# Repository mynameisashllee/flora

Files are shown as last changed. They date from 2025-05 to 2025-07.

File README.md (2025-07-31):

# flora
a big crepe paper flower that blooms the closer you get to it and closes up when you're further away!

i wanted to make it because i make a lot of pipe cleaner/paper flowers so i was wondering if there was a way to make my flowers a hardware project. after some deliberation i figured this was a pretty fun thing to do for my first arduino project! i get to make it huge and pretty and crafty too, which is great.

## build
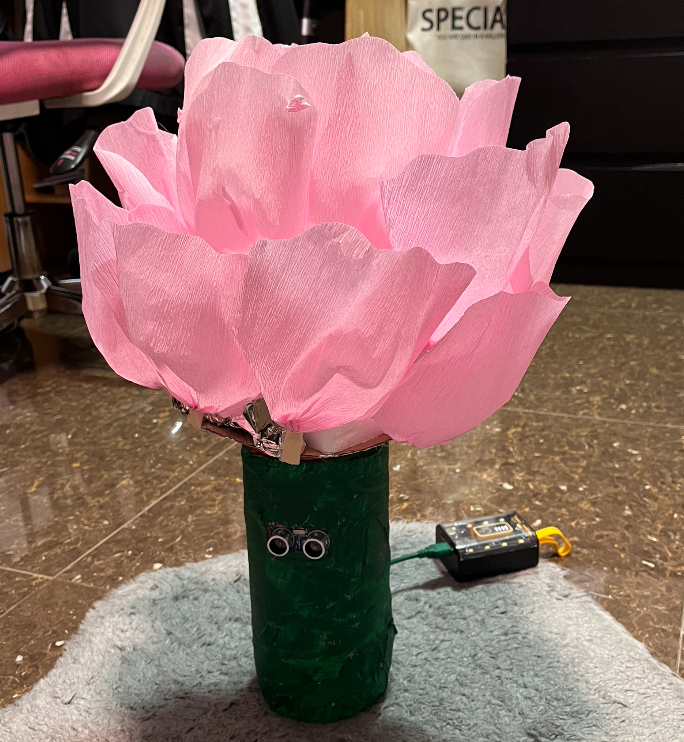
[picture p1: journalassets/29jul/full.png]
working


check out the demo on [youtube!](https://youtu.be/ohb0CGSC3Qs)

## screenshots
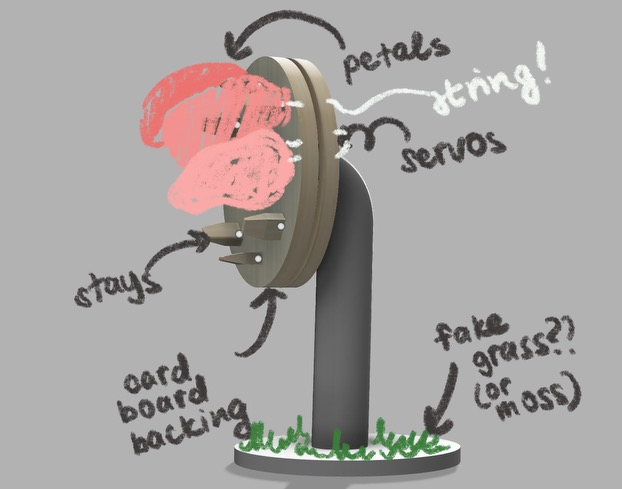
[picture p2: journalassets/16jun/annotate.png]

render of how the whole thing was planned to look - it's been changed up a bit!

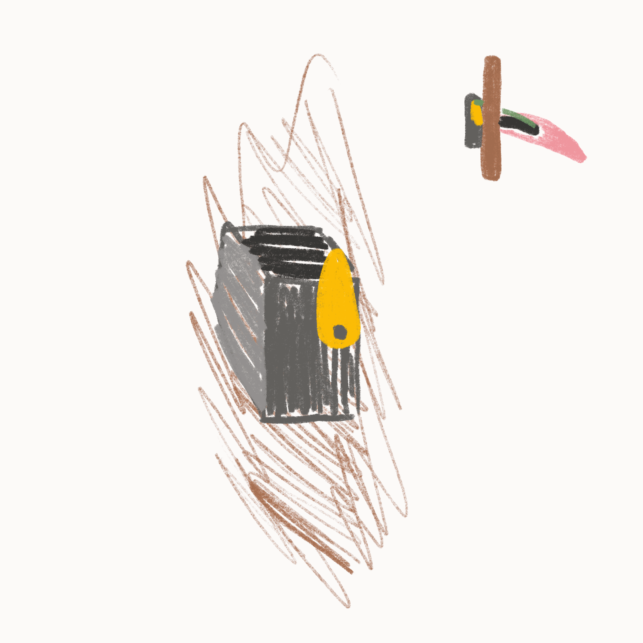
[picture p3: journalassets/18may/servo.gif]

how the servos turn

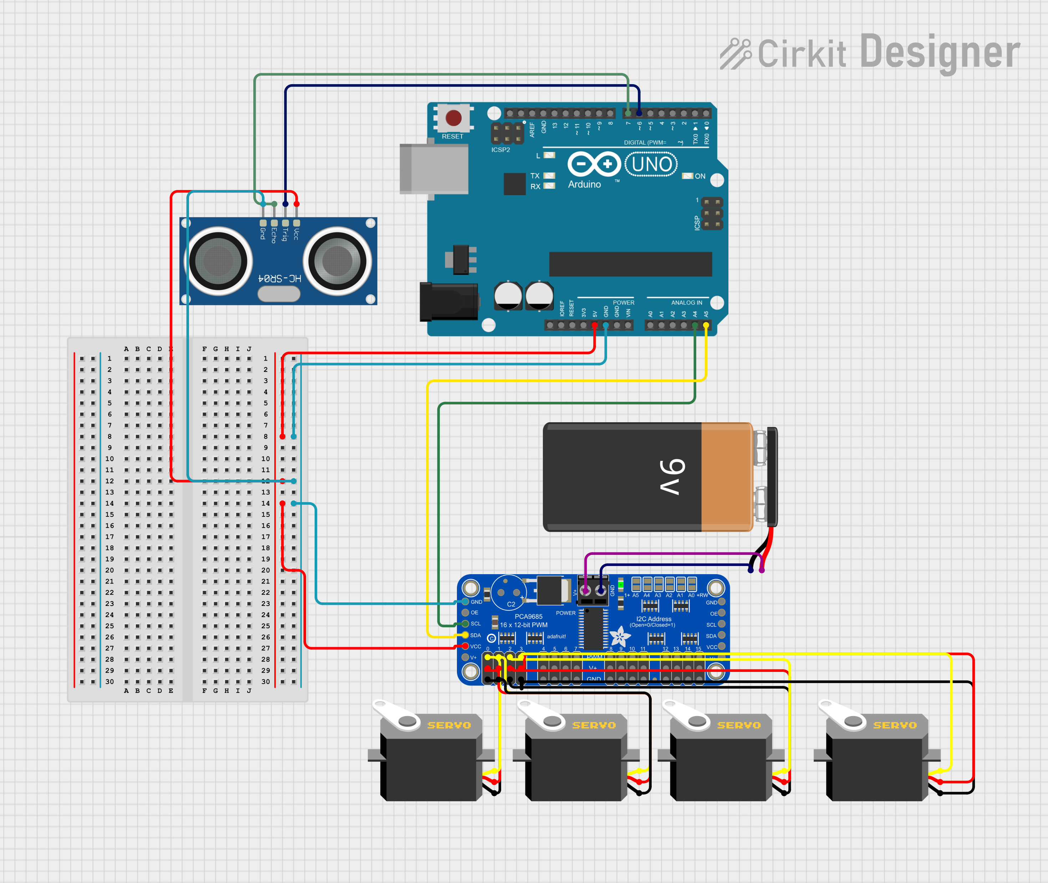
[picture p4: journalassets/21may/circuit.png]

wiring my arduino (4 aa batteries for power)

## bom
| **item name** 	| **purpose** 	| **qty** 	| **item source** 	| **item price** 	| **total price** 	|
|---	|---	|---	|---	|---	|---	|
| collar stays 	| holding up petals 	| 8 	| https://www.aliexpress.com/item/1005004401992941.html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 	| 1.78 	| 1.78 	|
| italian crepe paper (250x50cm) 	| petals 	| 5 	| https://www.aliexpress.com/item/1005007856841976.html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 	| 1.54 	| 7.70 	|
| fishing line 	| connecting petals to servo 	| 1 	| https://www.aliexpress.com/item/1005002121145052.html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 	| 0.80 	| 0.80 	|
| cardboard 	| base for flower parts 	| 1 	| recycled! 	| 0 	| 0 	|
| arduino uno 	| board to control other components 	| 1 	| https://www.aliexpress.com/item/1005007335850929.html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 	| 2.47 	| 2.47 	|
| PCA9685 16 channel driver 	| amplifying signal for servos 	| 1 	| https://www.aliexpress.com/item/1005005670283526.html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 	| 2.37 	| 2.37 	|
| breadboard 	| connecting components 	| 1 	| https://www.aliexpress.com/item/1005007174397080.html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 	| 1.17 	| 1.17 	|
| jumper wires (3 types) 	| connecting components 	| 20 x 3  	| https://www.aliexpress.com/item/1005007072081464.html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 	| 2.45 	| 2.45 	|
| HC-SR04 ultrasonic sensor 	| sensing distance 	| 1 	| https://www.aliexpress.com/item/1005007849944952.html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 	| 1.28 	| 1.28 	|
| MG 996R servos 	| to move the large petals 	| 4 	| https://www.aliexpress.com/item/1005004551732414.html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 	| 12.60 	| 12.60 	|
| battery case 	| to hold batteries 	| 1 	| https://www.aliexpress.com/item/4000859859685.html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 	| 0.98 	| 0.98 	|
| 4.7V batteries 	| to power servos 	| 2 	| already have 	| 0 	| 0 	|
| **total + shipping** 	| 	| 	| 	| 	| **35.19** 	|

## inspo
i actually had this idea myself but upon googling for more help i found this wonderful inspiration and absolutely had to mention it - [the tiktok](https://www.tiktok.com/@ingawoods.waight/video/7220271294841998638?lang=en). she made it in a *weekend* and i'm trying to model how my project looks after hers! huge props. we love women in stem.

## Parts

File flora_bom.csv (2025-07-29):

item name | purpose | qty | source | item price (USD) | total price (USD)
collar stays | holding up petals | 8 | https://www.aliexpress.com/item/1005004401992941.html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 | 1.78 | 1.78
italian crepe paper (250x50cm) | petals | 5 | https://www.aliexpress.com/item/1005007856841976.html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 | 1.54 | 7.7
fishing line | connecting petals to servo | 1 | https://www.aliexpress.com/item/1005002121145052.html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 | 0.8 | 0.8
cardboard | base for flower parts | 1 | recycled! | 0 | 0
arduino uno | board to control other components | 1 | https://www.aliexpress.com/item/1005007335850929.html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 | 2.47 | 2.47
PCA9685 16 channel driver | amplifying signal for servos | 1 | https://www.aliexpress.com/item/1005005670283526.html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 | 2.37 | 2.37
breadboard | connecting components | 1 | https://www.aliexpress.com/item/1005007174397080.html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 | 1.17 | 1.17
jumper wires (3 types) | connecting components | 20 x 3 | https://www.aliexpress.com/item/1005007072081464.html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 | 2.45 | 2.45
HC-SR04 ultrasonic sensor | sensing distance | 1 | https://www.aliexpress.com/item/1005007849944952.html?mp=1 | 1.28 | 1.28
MG 996R servos | to move the large petals | 4 | https://www.aliexpress.com/item/1005004551732414.html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 | 12.6 | 12.6
battery case | to hold batteries | 1 | https://www.aliexpress.com/item/4000859859685.html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 | 0.98 | 0.98
4.7V batteries | to power servos | 2 | already have | 0 | 0
total + shipping |  |  |  |  | 35.19

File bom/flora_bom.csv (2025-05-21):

item name | purpose | item source | item price | total price | qty
collar stays | holding up petals
italian crepe paper | petals
round mirror | centre of flower
fishing line | connecting petals to servo
cardboard | base for flower parts | recycled!
arduino uno | board to control other components
PCA968516 channel driver | amplifying signal for servos
breadboard | connecting components
jumper wires | connecting components
HC-SR04 ultrasonic sensor | sensing whether someone is there
MG 996R servos | to move the large petals
battery case | to hold batteries
AA batteries | to power servos
 |  |  |  | 0

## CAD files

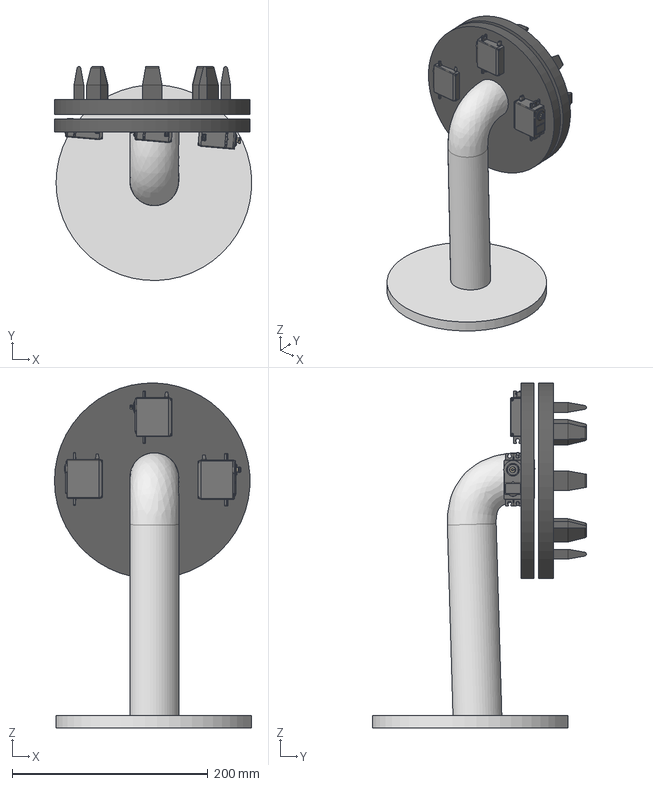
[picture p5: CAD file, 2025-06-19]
production/3d models/flora.step
201.5 x 218.7 x 352.7 mm

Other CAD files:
production/3d models/flora.3mf
production/3d models/flora.stl

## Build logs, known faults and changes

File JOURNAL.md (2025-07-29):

# journaling my journeying (33h total)

## 18-19 May (not very specifically documented sorry. i forgot)

okay! my idea for this whole project is basically a big ol pretty flower that opens up when you stand near it (so, arduino with distance sensor). i spent some time coming up with this idea because i really love making crafty flowers. i regularly make pipe cleaner/chenille and crepe paper flowers for my friends and birthdays and stuff!

if you don't believe me, here's my reference from valentine's day last year:
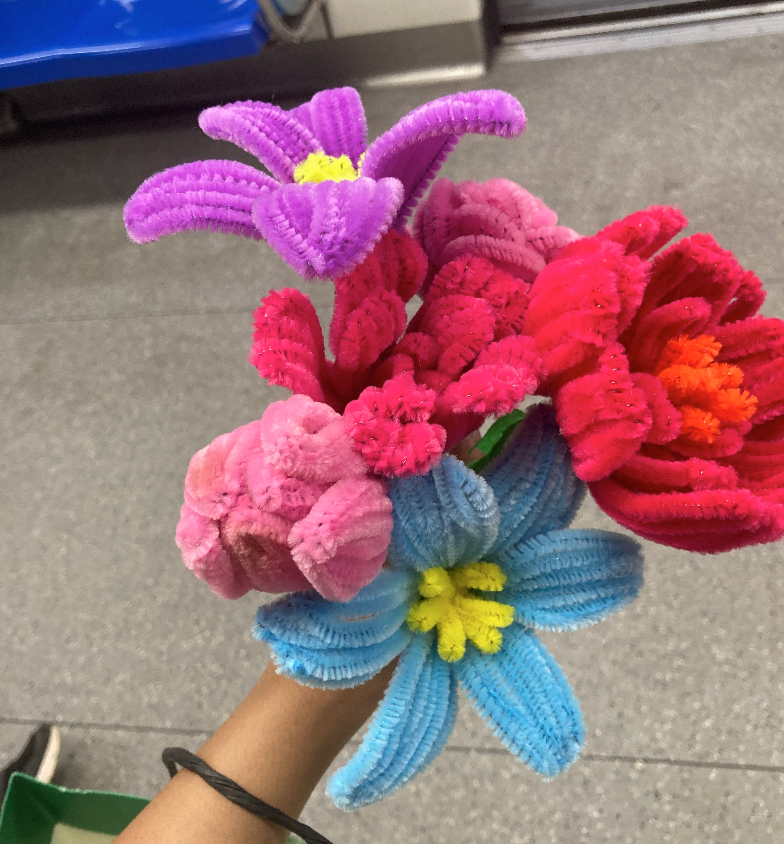
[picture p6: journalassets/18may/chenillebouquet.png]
bouquet


so i figured i'd motorise something like that. i found some stuff online like on pinterest but those flowers are like secretly protected by their makers so i'm going to have to improvise probably. i'm thinking of using an arduino, distance sensor and some servos.

this project is fairly mechanical, which means it's out of my pay grade for now. but we're here to learn! and of course my first step was to make a paper prototype-ish out of free foolscap i got handed outside my school.

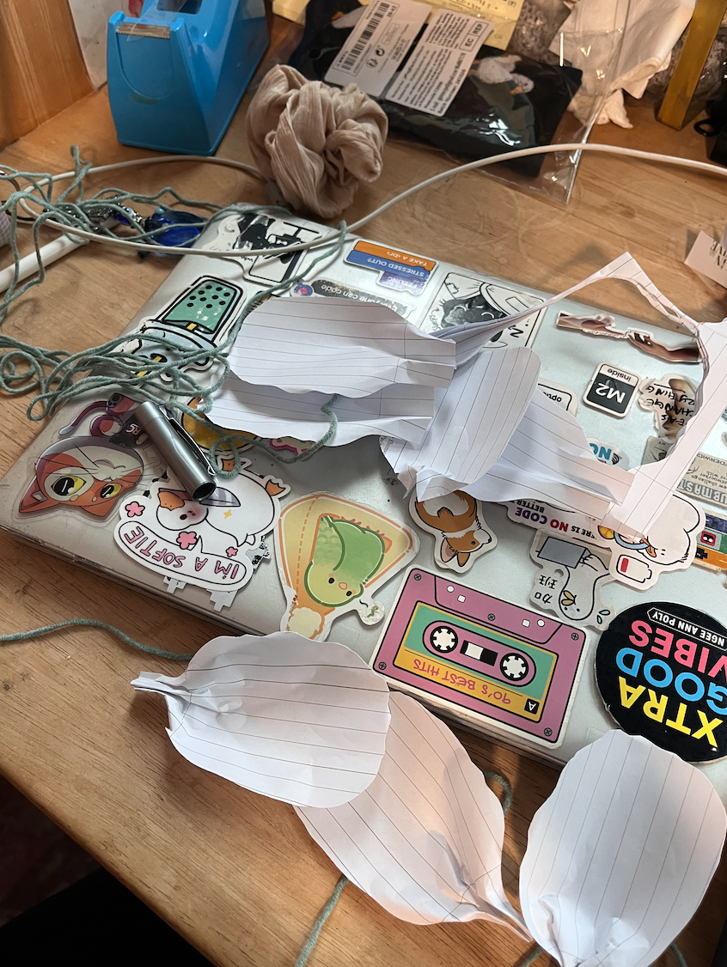
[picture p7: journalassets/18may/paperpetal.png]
paper petal

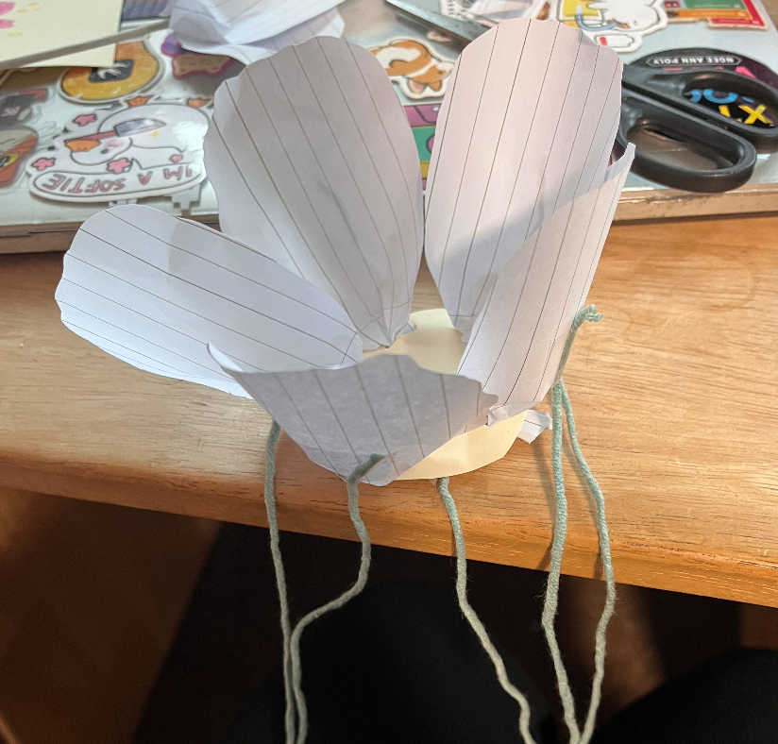
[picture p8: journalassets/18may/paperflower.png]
paper flower


so i cut out some rough outlines, attached it to a circle and tied some string. then i tried playing around with it to figure out how the servos could get it to open and i got a rough idea. 

animation!

i think for the actual thing instead of directly attaching the petals i'd want to use some bendy but half rigid plastic so it can snap back into place. because when i bend out the paper it crumples and doesn't go back to normal. and i think the string can be tucked into the circle too (maybe a bigger circle of foam board or smt) so there's more structure

alas, when i left for school and returned my paper flower was nowhere to be seen ): i guess someone assumed it was trash. rip

i guess over the next few days (or, i mean, after wednesday when i have an exam) i'd want to draw up a proper list of everything i need, wiring diagrams and maybe.. (ew) go on fusion.

update: i found a tiktok video of someone who actually did the same thing the internet is crazy. she put a mirror in the centre of the flower. i think that would be really cute.

time spent: 4 hours

## 21 May
just had an exam! yay! 2 things to do today - wiring and my bom

we did some wiring practice today - aka i learnt how to wire arduino stuff and got super intimidated. but it's actually not that deep surprisingly. i also found the models for the parts i plan to use which is good because bom!

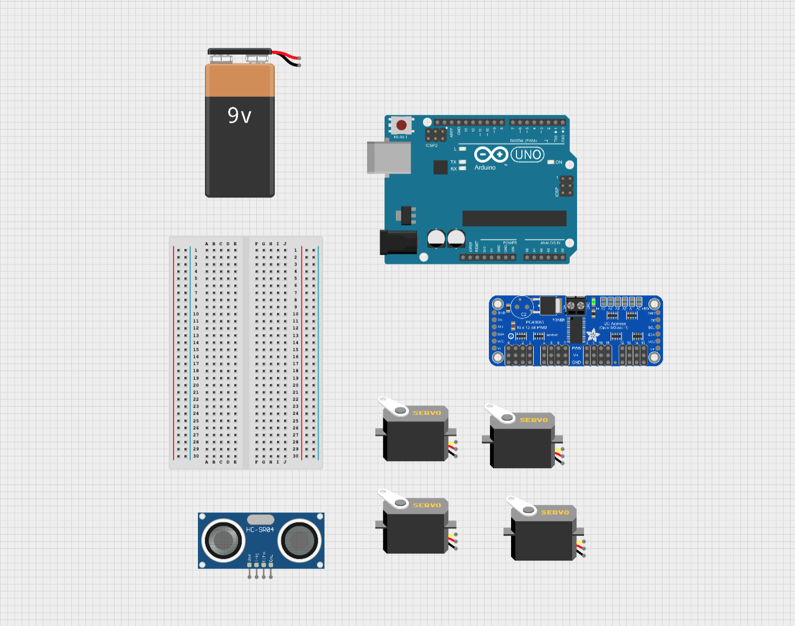
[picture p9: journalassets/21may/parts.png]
parts


after googling a bunch and looking through a lot of other peoples' arduino wiring designs i got this abomination (actually, this wasn't the worst. this was halfway through me detangling it)

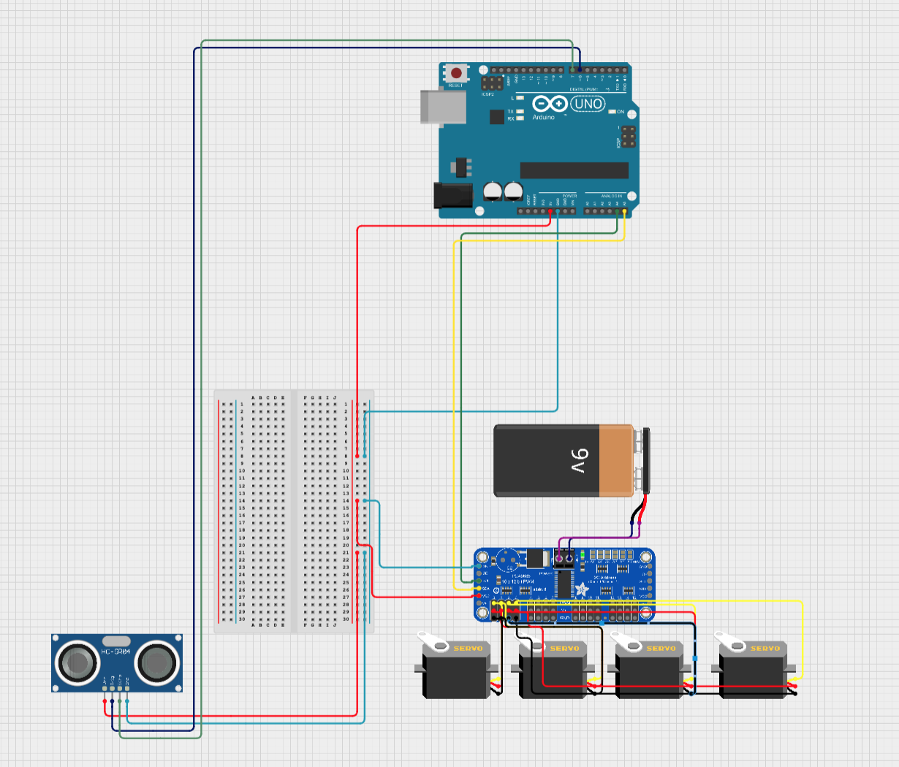
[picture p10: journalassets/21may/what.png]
oh


what the heck. i'm so sorry you had to see that.

anyway, we did it! 
final

not actually using a 9v battery, 6v instead (4 aa batteries) which hopefully works..! i panicked a lot about this and went to my friend who's on the school robo team for advice but she said it was okay
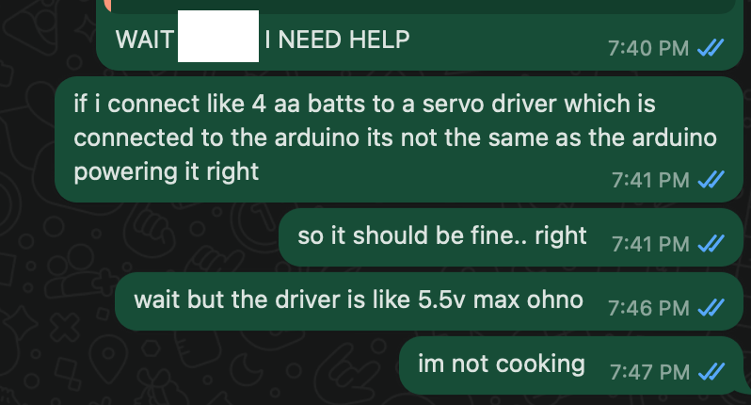
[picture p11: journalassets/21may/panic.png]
panic


things i learnt:
- connect everything to ground and 5v on the breadboard
- dont connect power to arduino

and did the bom too (sort of, lol)

time spent: 3 hours but spread out

## 16 Jun
oops, it's been a while.

today i finally bothered to 3d model the design - the *rough* design. i'm thinking of using acrylic pipes to connect flower and base because it will likely save me a lot of time on modelling and deciding the size.

here's me going absolutely insane while modelling because it took REALLY, REALLY long!
panic

anyway, this should basically show the structure of how my project will look. since a lot of my materials are like paper/cardboard/pipe, i don't want to be very exact with it because it'll likely take some trial and error to get it right. hopefully these dramatic shots (and my 3d model) can give a rough overview, though!

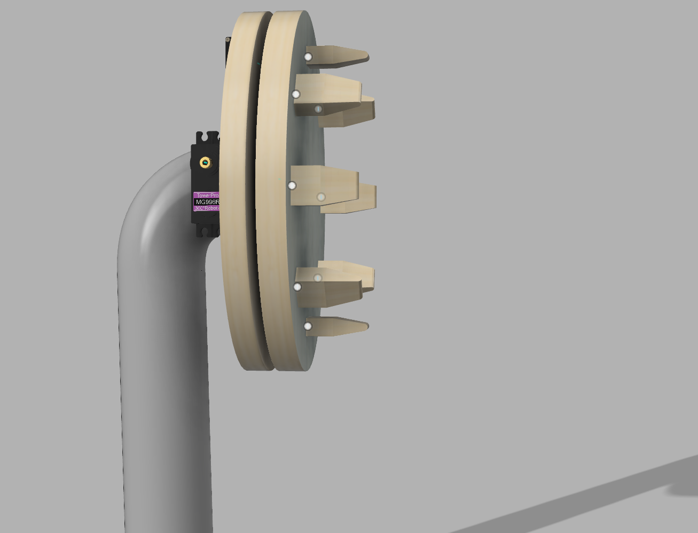
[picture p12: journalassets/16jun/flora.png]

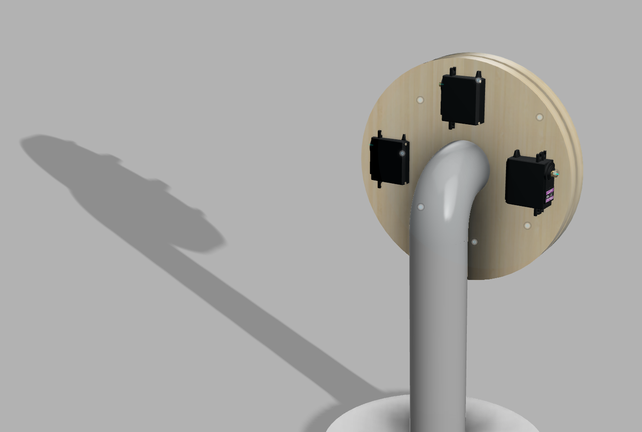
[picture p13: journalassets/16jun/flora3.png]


there are 8 props that will be used to hold up the petals, and string will attach the petals to the servos through the big cardboard centre. i wasted a lot of time trying to model the petals but here's a handy diagram of how they (and everything) should look.

diagram

i also did my firmware...! everything is in the production folder including wiring. truly appreciating online tutorials because they made my code and it's been forever since i used c++. i get why my friends who do robotics crash out all the time. i suspect that will be me soon.

next up i will finalise my bom... when i have the time.

time spent: 5 hours

## 17 Jun

took a break from studying today to finish up my BOM!

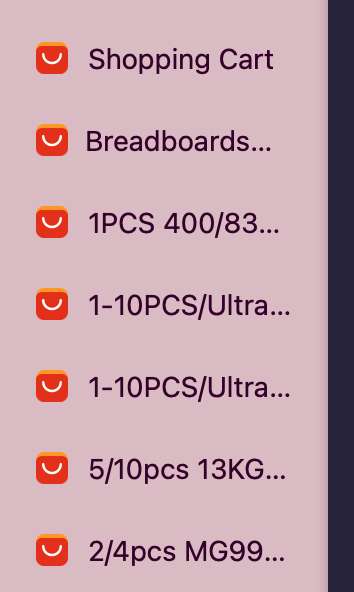
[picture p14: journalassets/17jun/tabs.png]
tabs


it has been done. i think i might submit now after a final few checks!

time spent: 1 hour

## 27 Jun

building!! my parts are all here and i was super excited to start.

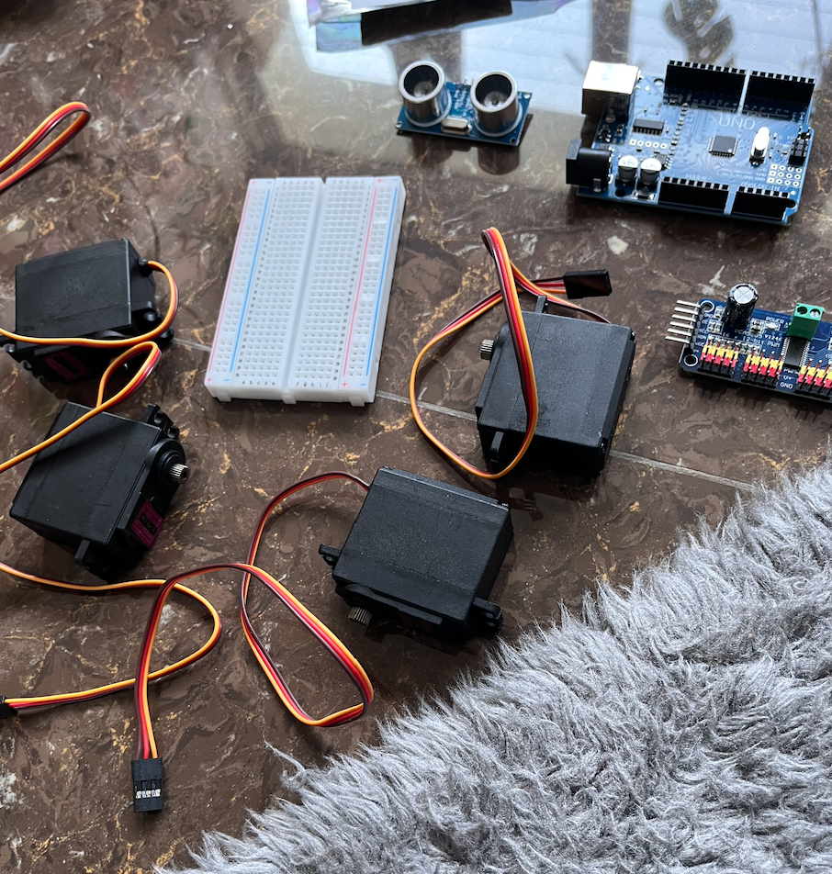
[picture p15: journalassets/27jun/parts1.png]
parts


first order of business was making sure my electronics work. so i took everything and wired it according to my diagram.

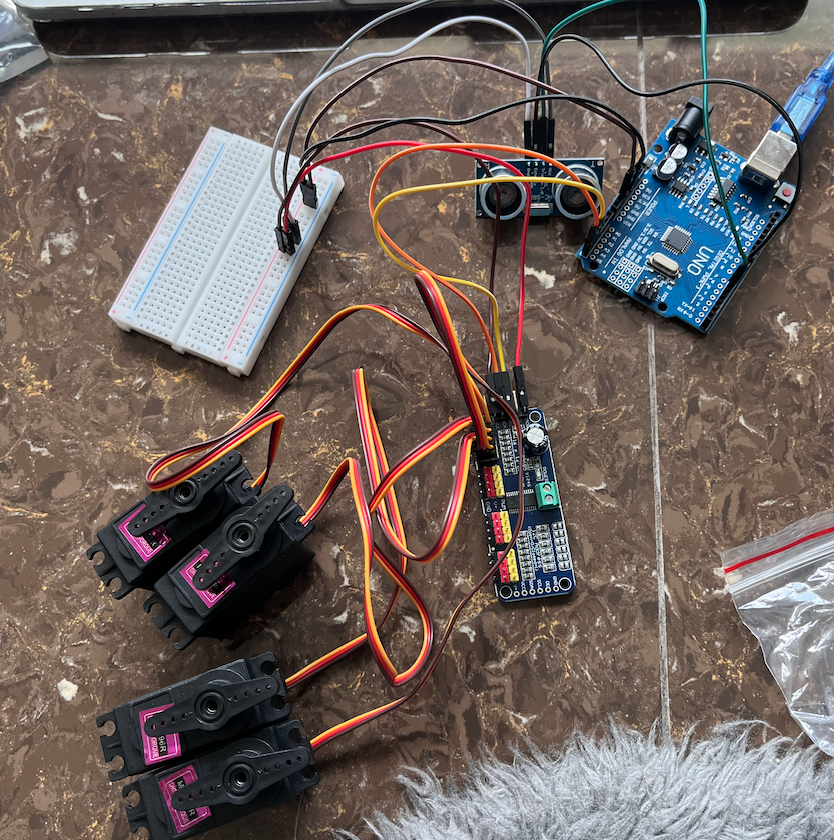
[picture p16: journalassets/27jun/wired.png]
wired


so initially i was freaking out because when i uploaded my firmware: 1. there were syntax errors (thanks c++) because i forgot semicolons and variable definitions like everywhere 2. MY SERVOS DIDN'T WORK 

so i started on debugging and i realised that, like a fool, i had forgotten to link up my pwm drivers to my battery pack! aha! what a great solution, i thought to myself, pulling out my battery case for 4 aa batteries. turns out i had ordered the wrong one. it was for much bigger 3.7V batteries.

in order to actually test my code and stop crashing out i just linked it to the arduino and disconnected it from power like every 20 seconds while hoping it didn't get fried. i'll probably go get some normal battery packs soon. i'm also regretting getting such short wires because i'm not super sure how everything's going to look on the whole flower structure BUT whatever.

once my servos worked, i had some more logic errors which made the servos reset every time they ran the open and close functions 

janked

(????)

so i set out to fix it with some irritating comments

code

after a bunch of hard work, here are my servos... working as intended! i'll probably have to cut the servo horn in half before i start assembling so it doesn't hit the cardboard.

working

also my crepe paper is here too, with surprisingly good quality. here's a petal model which is how it will look on the flower! (but bigger, probably)

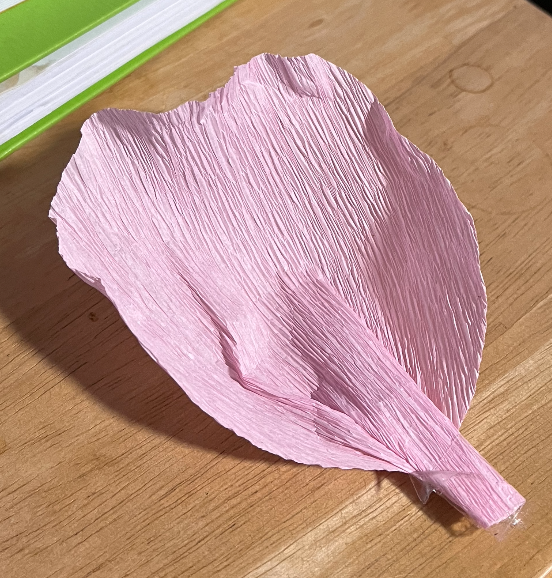
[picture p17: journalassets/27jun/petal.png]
petal


i spent a lot of time on the floor today. my knees hurt. i stabbed my finger with a pen. back for more next time.

time spent: 4 hours

## 5 July 
now that my circuit was ready, it was time to begin. today was the day i would finish it all. (or the base, anyway.) 

first off, i decided to actually cut the servo horns. using the power of wire cutters and sheer brute strength, i actually managed to do it all myself! 

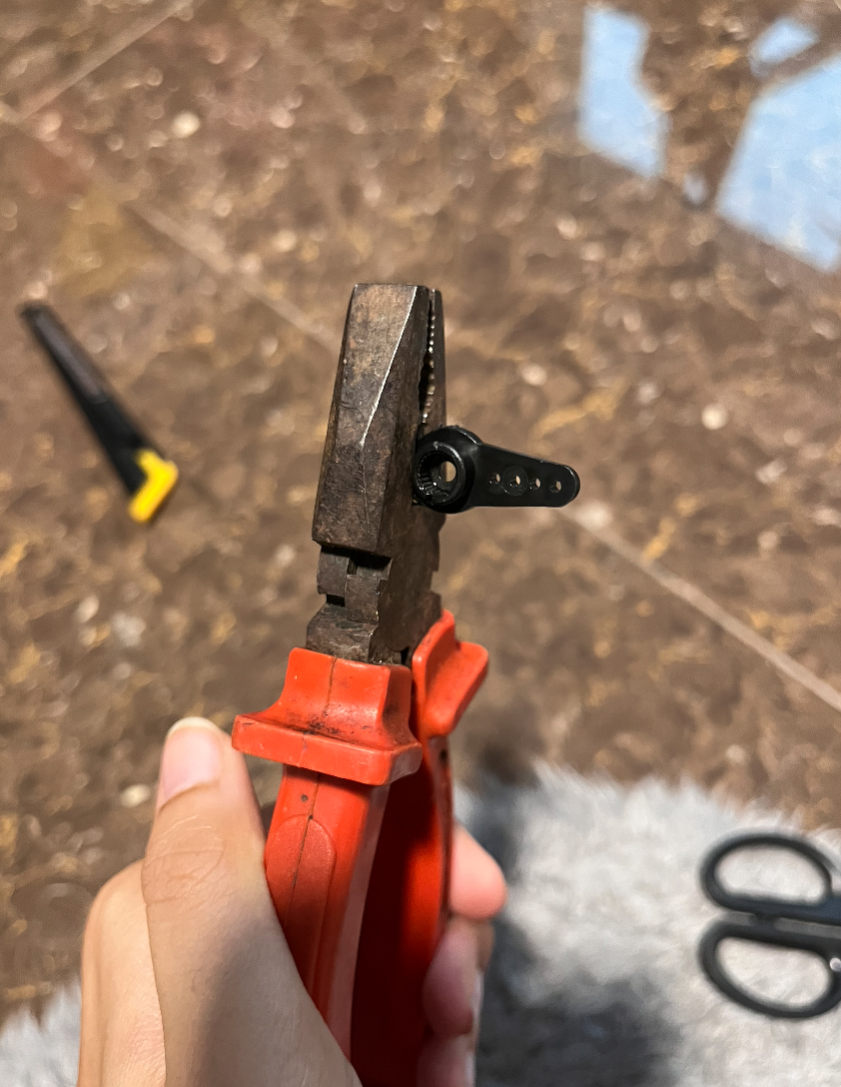
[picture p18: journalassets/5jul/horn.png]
horn


my hands were very, very red afterwards. i definitely do not recommend this step and if you ever find one sided servo horns you should just use those instead.

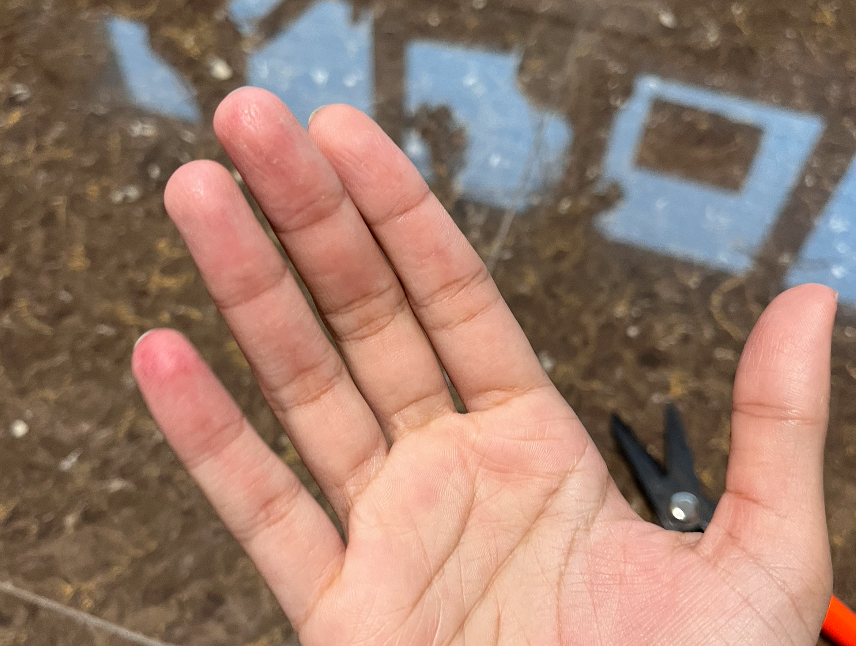
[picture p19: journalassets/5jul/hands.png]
hands


next, i scoured through my house for spare cardboard, and we had some nice thick boxes! the only problem was that there were folds at the places where i wanted to cut out the circle, but i figured i'd double layer the cardboard to make it sturdier.

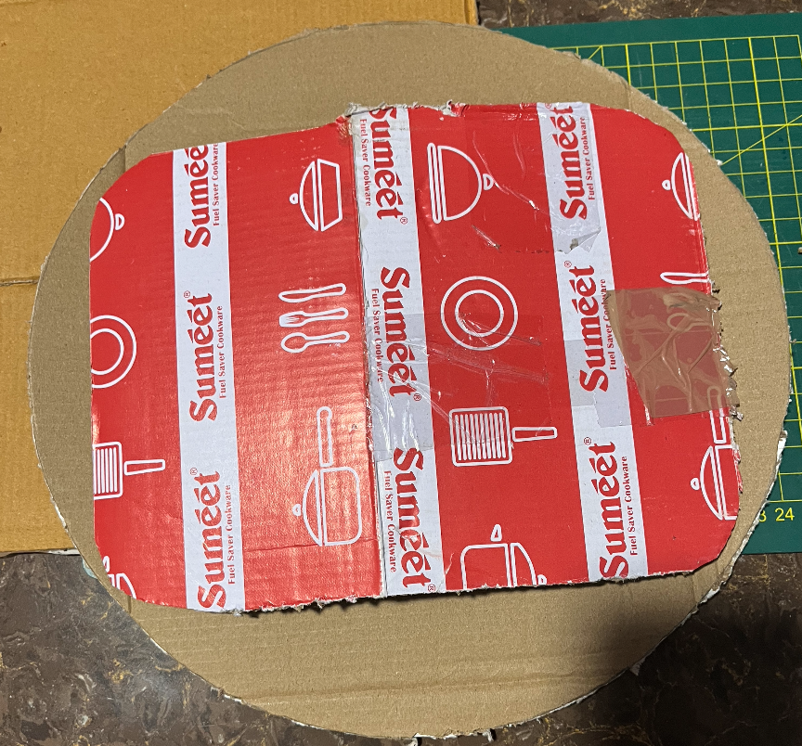
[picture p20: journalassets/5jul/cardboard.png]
cardboard


then i laid out the servos in the intended circlular orientation to figure out the correct way to open and close the petals. i made this high quality diagram to show the directions of the servos when the flower is 'open' for reference.

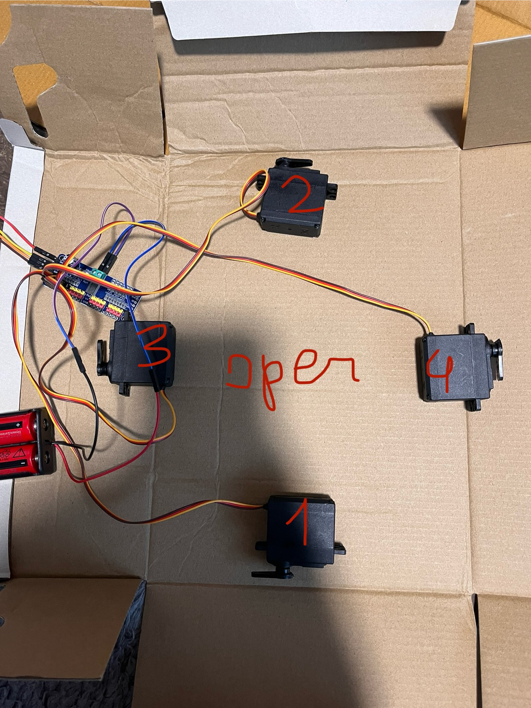
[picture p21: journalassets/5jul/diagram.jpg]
diagram


i then took to my collar stays with a heated screwdriver (the sad part was that it's a magnetic screwdriver with different heads and i think i ruined the magnetism by heating it) and poked some holes in them to tie the string. 

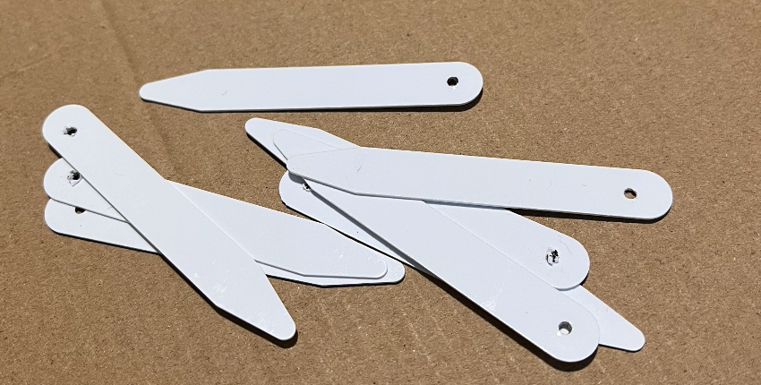
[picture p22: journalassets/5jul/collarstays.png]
collarstays


assembly time!! i taped the servos in positions and tied two collar stays to a servo with the fishing line. 

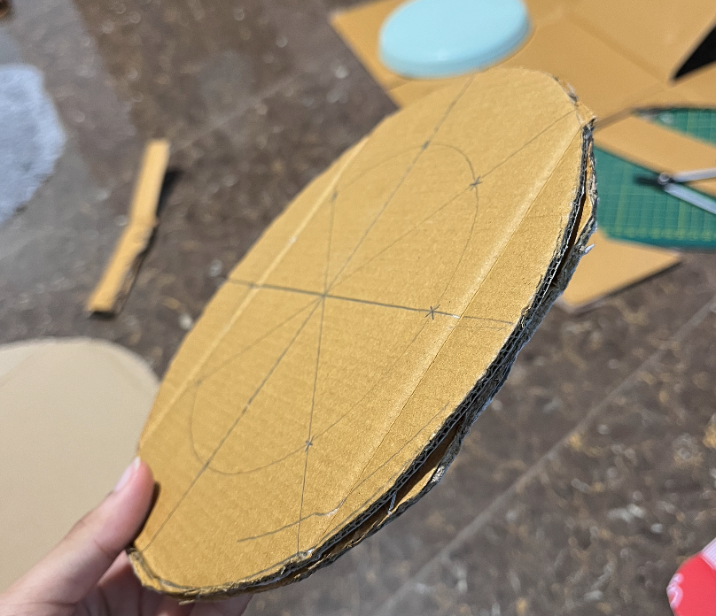
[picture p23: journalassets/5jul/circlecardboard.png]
circlecardboard


https://github.com/user-attachments/assets/06558860-657e-401c-917a-8a24dc6fcc48

when i powered up the servos i was like, woah! this is so cool! it works! 

https://github.com/user-attachments/assets/97546c10-0c78-4bb9-bc74-a5d542ef6f94

then i went oh no, because only half the collar stays were being pulled open. after analysing the front and back i realised that the servos were in a position where they were closer to one of the collar stays, so there wasn't an even distribution of torque between the two and one of the collar stays just closed up more.

once i fixed the orientation, i realised that my cardboard circle was really small and the servos would just knock into each other so i elevated two of them with a hot glued contraption of spare cardboard.

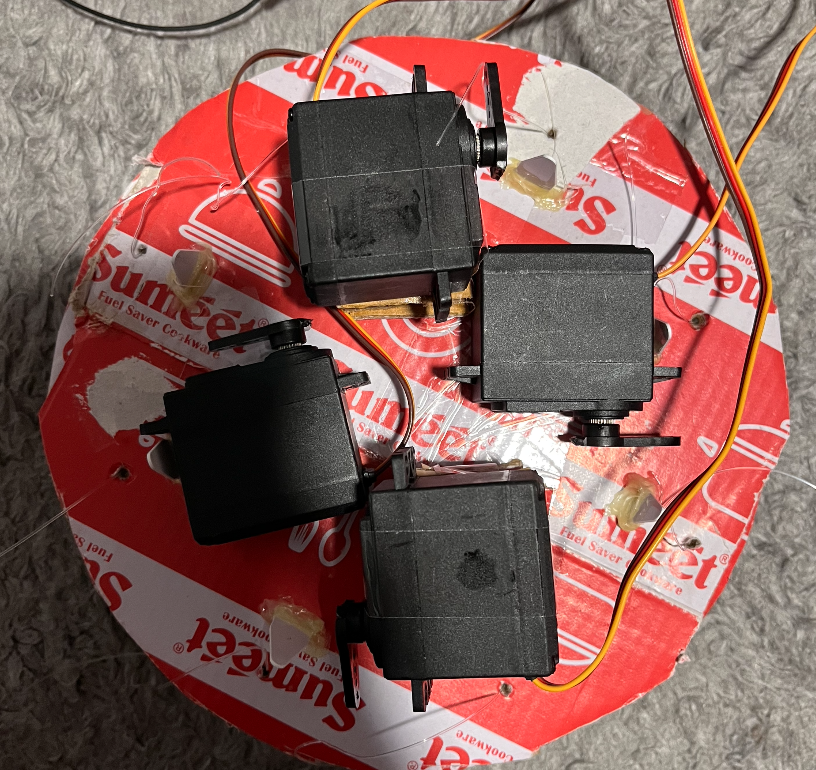
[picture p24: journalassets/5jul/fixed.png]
fixed

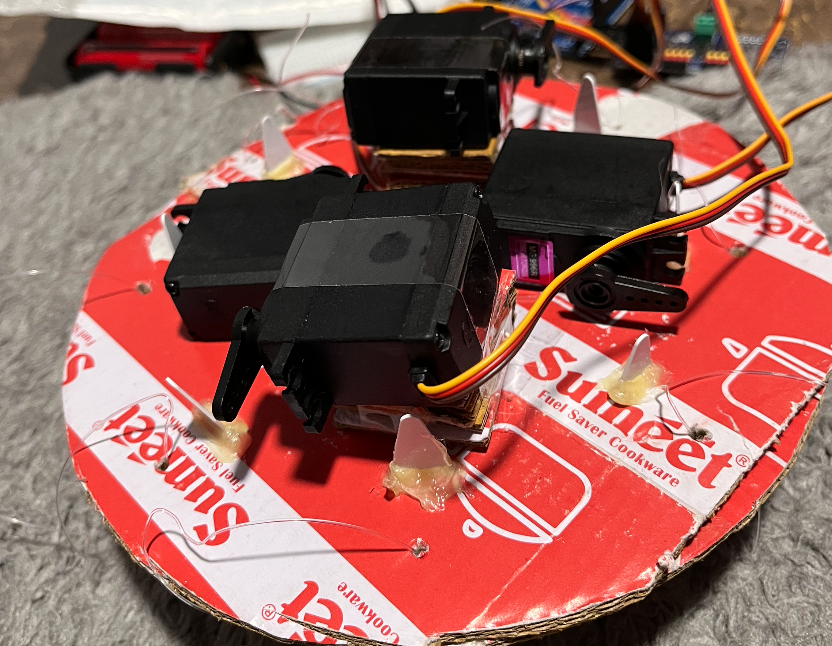
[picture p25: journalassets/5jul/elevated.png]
elevated


and voila!! it worked.

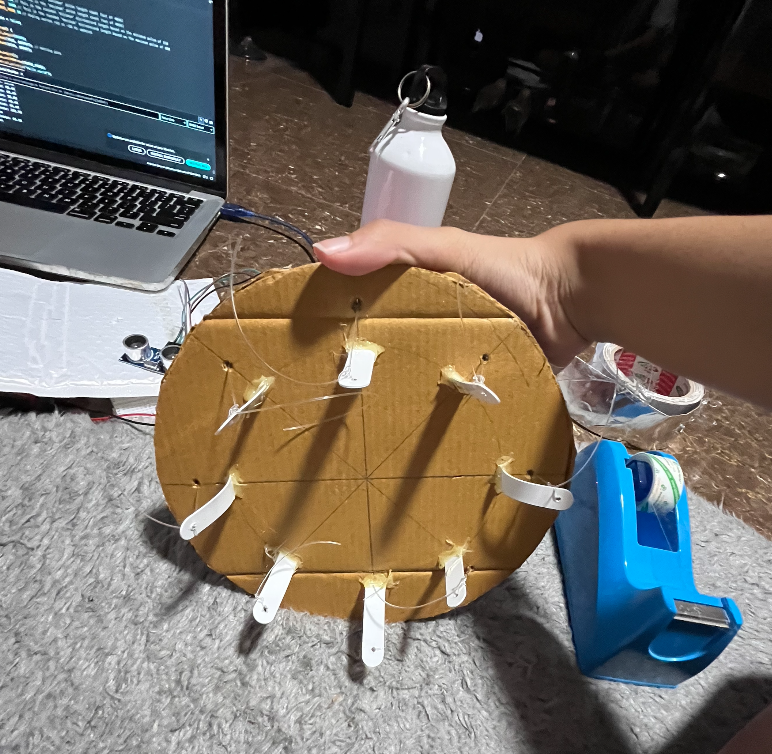
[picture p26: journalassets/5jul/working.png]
working


then i got to work securing everything properly with hot glue and my circuit kind of came apart. suddenly... once i rewired everything the servos JUST STOPPED WORKING. they heated up a lot and just didnt move at all even though power was going through the circuit. at this point it was 12am, and i was crashing out and just let it go. good night.

(8 hours)

## 7 July
so after consulting with the slack, i got really terrified that my servos were just totally fried. after checking my wiring properly i realised that i had just wired my servo driver into the wrong GPIO pin on my arduino. i felt like a fool. on the bright side, it works now! properly! but no day comes without its challenges, and today's challenge was that i tied some of the fishing lines too tight so one of the servos just popped off the base and some of the lines snapped. but once i fix this, it'll definitely work!

## 22 July
my first entry after getting back from undercity! i retied my lines and hot glued AND taped my servos properly to really ensure they stayed in place (because the cardboard stack i put the servo on was not stable enough. but now it is!).

and then on to my favourite (crafty) part... the petals! here's my flower with one attached.
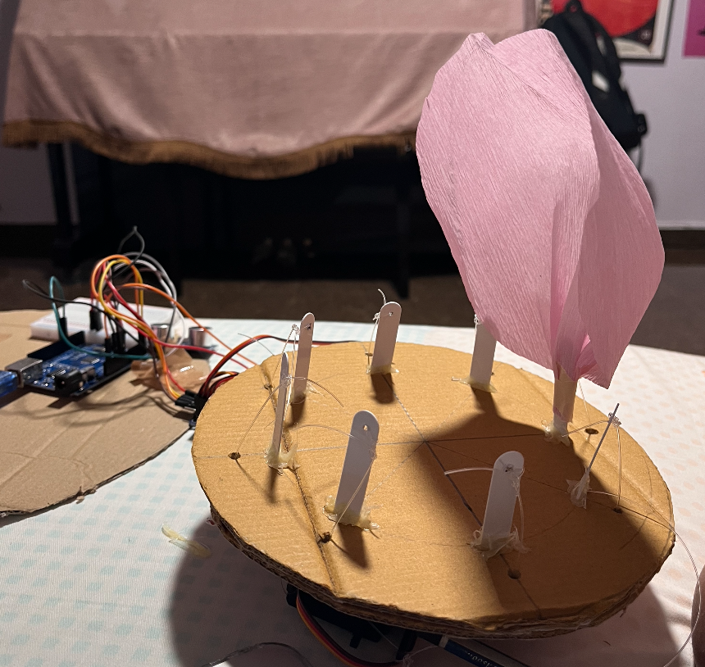
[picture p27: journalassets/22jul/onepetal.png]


and here's all 8 of the moving petals! in action!! i'm so excited honestly.

https://github.com/user-attachments/assets/9ec3462b-fdc6-45b9-ad6f-49686b10f35d

i think my next problem is like... worrying about how i'm gonna find a stand and. put it together. maybe i'll find some old lamp like someone suggested and stick the components on the back where they can't be seen or something.

(2 hours)

## 27 July
okay! i've officially decided on this old bottle. 

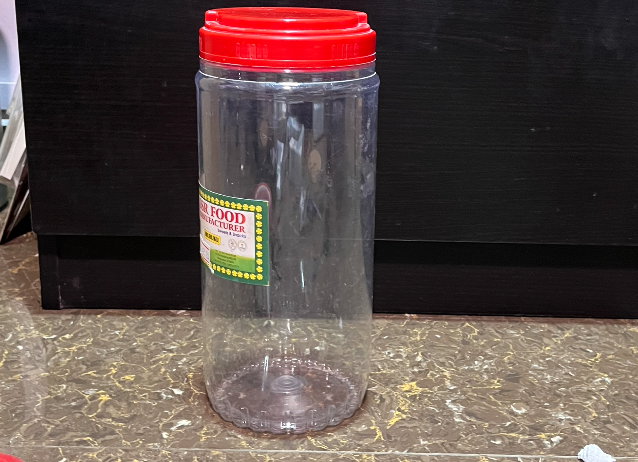
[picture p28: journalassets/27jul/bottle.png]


i guess this project is gonna be eco friendly because i've been using a bunch of recycled cardboard too. i was kind of apprehensive about this being my stem because it was kind of thick but i realised it can hide all my components inside. which is pretty much a win.

so first i taped up my servo wires, and cut up some styrofoam (which makes a really irritating noise) because i had to make a sturdy structure for the whole flower to sit on. (i also nixed the sideways design because. no materials. no time. it'll be upright now)

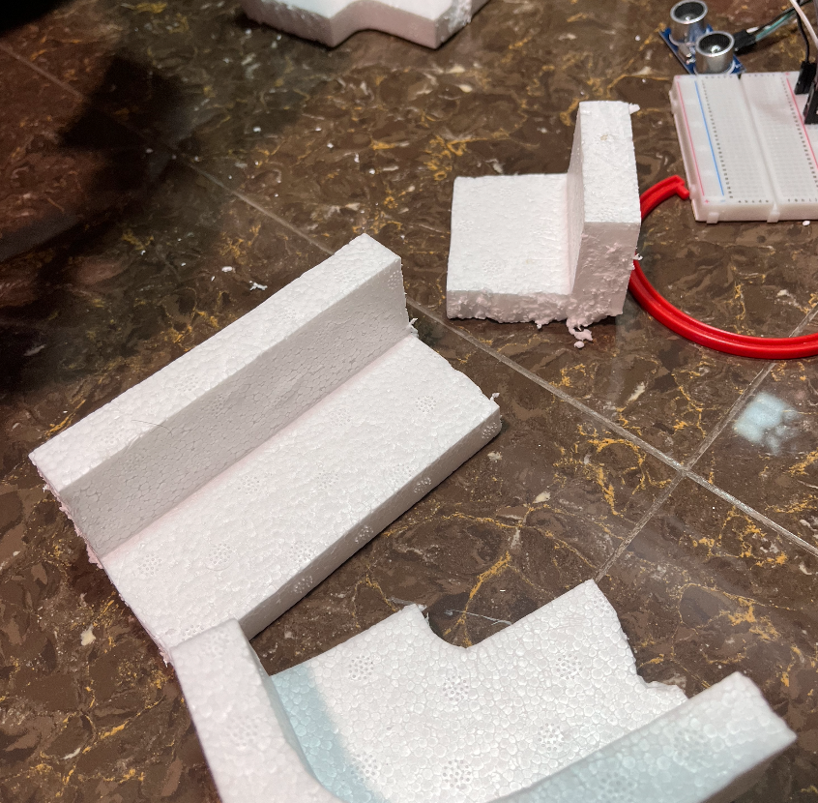
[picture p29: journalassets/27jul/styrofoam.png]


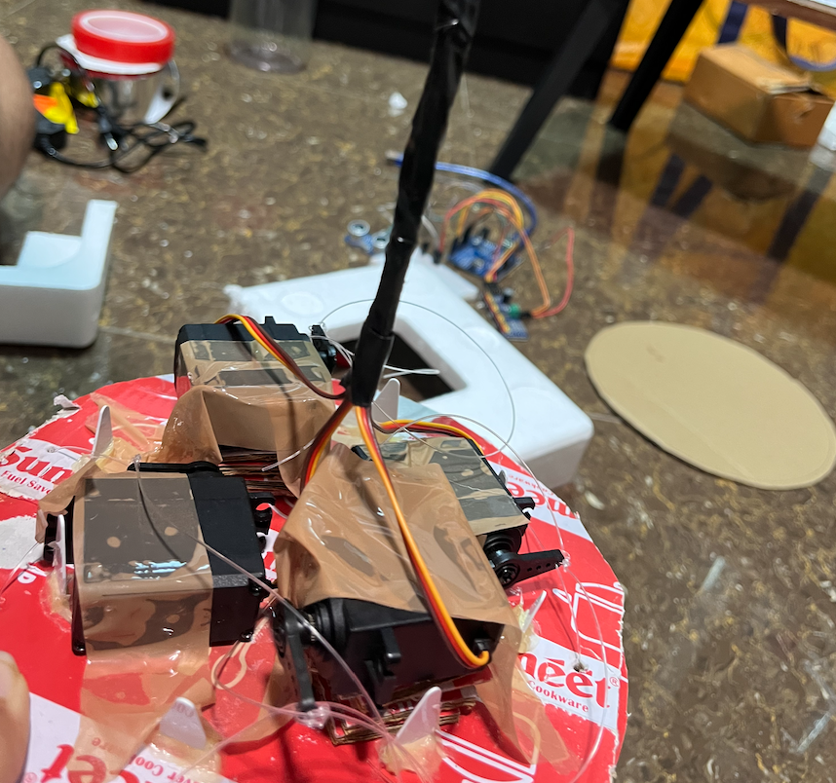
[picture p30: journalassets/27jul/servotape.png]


here's the final structure, which i glued onto the lid of the bottle. i also used my messed up soldering iron tip to poke a hole into the lid for the servo wires to go through. and here it is semi-assembled. what a beauty.

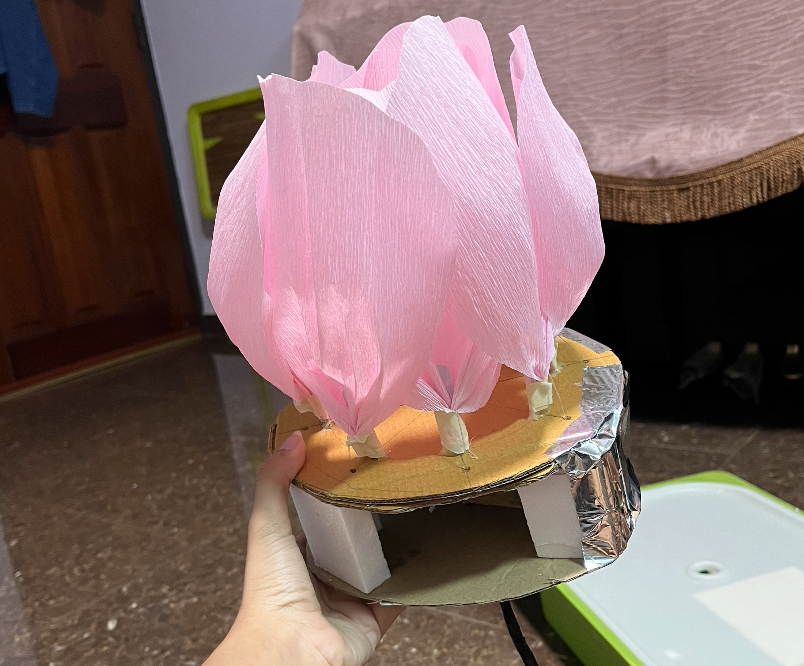
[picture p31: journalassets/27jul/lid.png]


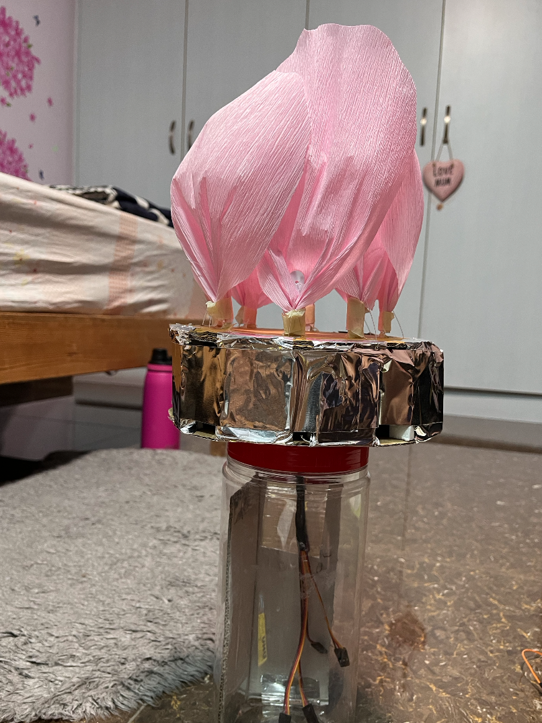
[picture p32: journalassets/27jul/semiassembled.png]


i also decided to take a chance on my soldering skills and solder the battery wires because they were really unstable connections when i used the jumpers. and it worked! i love soldering. so right now the 4.7v batteries power the servos and an external source (power bank/laptop) powers the arduino.

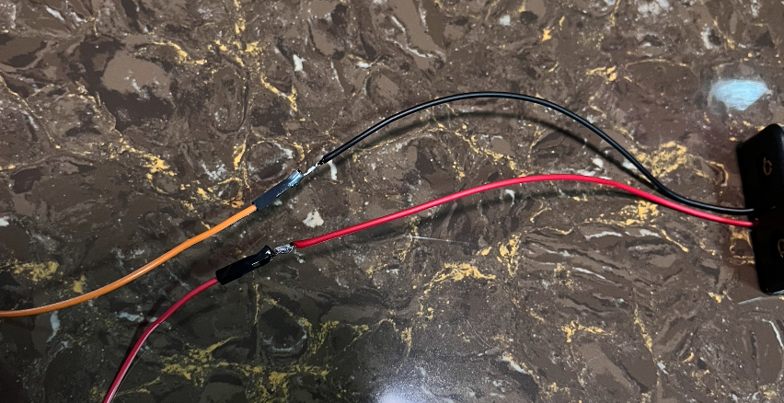
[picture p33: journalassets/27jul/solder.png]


also, i stuck all the other circuit components on cardboard to fit inside the bottle neatly. so i taped up and hot glued my jumper wires to make this slightly cryptid-looking thing.

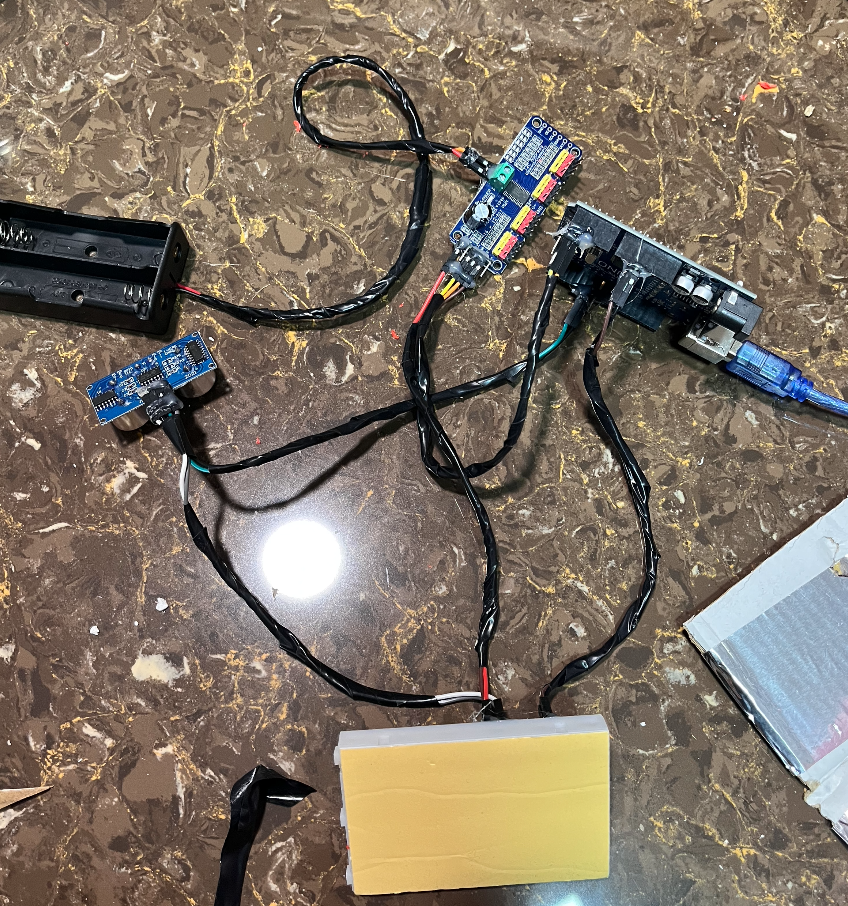
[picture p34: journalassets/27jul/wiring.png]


of course, the distance sensor has to peek out, so i cut (melted) out a hole for it.

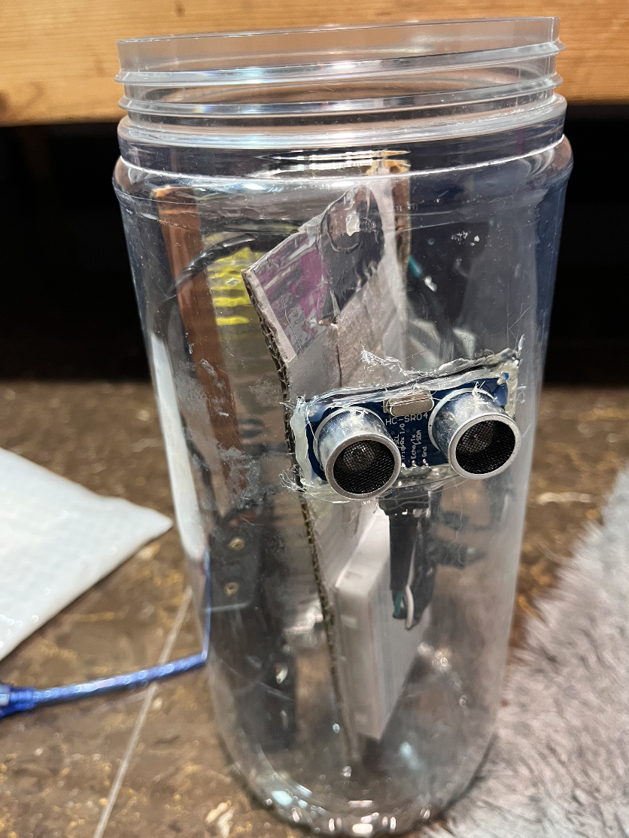
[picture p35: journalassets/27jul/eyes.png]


with the distance sensor 'eyes' and the arduino cable 'tail' it kind of looks like a woodland creature with a flower hat, which is pretty cute honestly. and i also wrapped the whole thing in masking tape so it'd be easy to paint! (it still took very long, but it was less painful, i guess). and here's my final product for the day.

working

after this, i started freaking out because the thing suddenly wasn't working! but it turned out to just be the batteries running out of juice. which is easily solvable because they're rechargeable (: yay

(4 hours)

## 29 July
the final stretch! i spent a while painting the whole stem (and arduino cable) green, tested the flower again with charged batteries to make sure it worked, and began cutting, like, 10 more big petals.

working

i also made a mini rose structure to fill up the middle space.

working

here's the whole thing!

working

and here's it open and closed from the top view. 

working

working

it's so pretty. i'm also so happy it's finally done. BYE BYE! like and subscribe.

(2 hours)

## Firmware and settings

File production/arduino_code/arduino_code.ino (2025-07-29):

#include <Wire.h>
#include <Adafruit_PWMServoDriver.h>

Adafruit_PWMServoDriver pwm = Adafruit_PWMServoDriver();

const int TRIG = 6; // distance sensor values (pins and threshold)
const int ECHO = 7;
const int DISTANCE = 150;

#define SERVOMIN  150 // This is the 'minimum' pulse length count (out of 4096)
#define SERVOMAX  600 // This is the 'maximum' pulse length count (out of 4096)
#define USMIN  600 // This is the rounded 'minimum' microsecond length based on the minimum pulse of 150
#define USMAX  2400 // This is the rounded 'maximum' microsecond length based on the maximum pulse of 600
#define SERVO_FREQ 50 // Analog servos run at ~50 Hz updates

bool isOpen = false;

void setup() {
  Serial.begin(9600);
  pinMode(TRIG, OUTPUT); // setting pins
  pinMode(ECHO, INPUT);

  pwm.begin();
  pwm.setPWMFreq(SERVO_FREQ);
  Serial.println("Hello world");


}

void loop() {
  digitalWrite(TRIG, LOW);
  delayMicroseconds(2);
  digitalWrite(TRIG, HIGH);
  delayMicroseconds(10);
  digitalWrite(TRIG, LOW);

  float duration = pulseIn(ECHO, HIGH);
  float distance = duration * 0.017;

  Serial.print("Distance: ");
  Serial.println(distance);
  // if dist < max, if not open, open it. if open, run open w return func
  // else if open, close. if close, run close w return func
  if (distance < DISTANCE) {
    open();
  } else {
    close();
  }

  delay(100);

}

void open() { //from 0 to 180
  if (isOpen) return;
  for (int pos = SERVOMIN; pos < 400; pos += 10) {
    pwm.setPWM(0, 0, pos);
    pwm.setPWM(1, 0, pos);
    pwm.setPWM(2, 0, pos);
    pwm.setPWM(3, 0, pos);
    delay(50);
  }
  Serial.println("open");
  isOpen = true;
  delay(5000);
}

void close() { //from 180 to 0
  if (!isOpen) return;
  for (int pos = 400; pos > SERVOMIN; pos -= 10) {
    pwm.setPWM(0, 0, pos);
    pwm.setPWM(1, 0, pos);
    pwm.setPWM(2, 0, pos);
    pwm.setPWM(3, 0, pos);
    delay(50);
  }
  Serial.println("close");
  isOpen = false;
  delay(5000);
}

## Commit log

2025-05-21 more journaling
    [flora_bom.csv]
2025-06-16 more journaling + fusion + firmware
    [flora.3mf, flora_bom.csv]
2025-06-16 small edits
    [flora_bom.csv]
2025-06-17 updated bom
    [flora_bom.csv]
2025-06-19 added step + stl files
    [flora.3mf, flora.step, flora.stl]
2025-07-29 journal updates
    [flora_bom.csv]
